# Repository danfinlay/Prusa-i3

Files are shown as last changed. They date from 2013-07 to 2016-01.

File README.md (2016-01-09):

# Dan's Prusa i3 Variant

I use this repository to store all the information I need on my 3D printer, an aluminum [Prusa i3](http://reprap.org/wiki/Prusa_i3), modified from a kit sold by *XS's Ink*, that I bought off Craigslist from a guy who had gave up at getting it working.

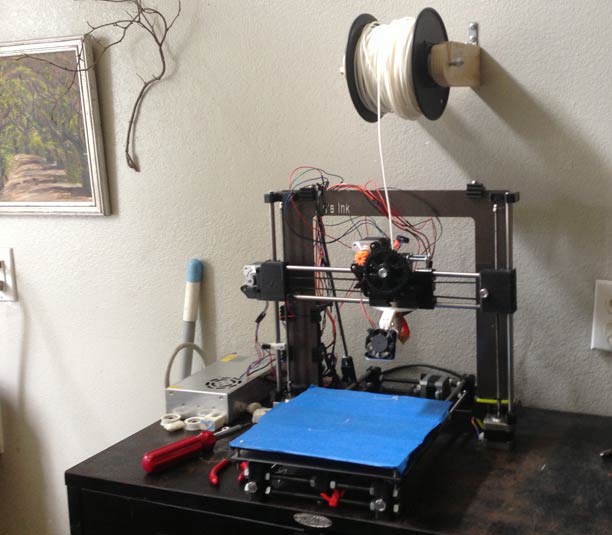
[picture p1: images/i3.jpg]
My printer


 - Model files to print the physical body.
 - Firmware files for flashing an Arduino (in my case, a [Sanguinololu 1.3a](https://github.com/mosfet/Sanguinololu/tree/master/rev1.3a))
 - Calibration files for use with [Slic3r](http://slic3r.org/).
 - Eventually I hope to add details on my OctoPrint server, maybe a Chef recipe. For now I have an SD image I clone, which is a bit bloated for version control.

## Physical Information

 - Size: 200mm cubed
 - Type: Aluminum framed body
 - Belt type: GT2 (2mm toothed robotics belt).
 - Extruder:  [Greg's Wade Extruder](http://www.thingiverse.com/thing:65939).
 - Nozzle: 0.5mm [Budaschnozzle 2.0](https://www.lulzbot.com/support/budaschnozzle-20) with 1.75mm PTFE tube modification for printing 1.75mm filament (I use PLA).
 - Bed leveling system: 3-point leveling, generally adjusted during the skirt-printing that occurs before every print when using the included Slic3r calibration bundle.

## Beware below!

Below is a pasted and only minorly cleaned up text file that I used to keep notes while I was originally calibrating the machine.

## Notes

serial frequency: 115200

micro step = 16x
full steps per revolution = 200
*This seems to be outdated, I use GT2 belts now:*
T5 belt (5mm) : http://www.sdp-si.com/D265/PDF/D265P1032.pdf
12 teeth on x & y motor gears

XY STEPS: 53

Z axis: M5 threaded rod (0.80 pitch).

Z STEPS: 4000
(un-micro-stepped gives us 0.08mm per step, the safest increment)
Set current z to 0: G92 Z0

### Valid layer height options
```javascript
for (var i = 0.2; i < 0.4; i+=0.08) { console.log(i); }
```
 - 0.2
 - 0.28
 - 0.36
 - 0.44

### Wade's Geared Extruder details:

hob diameter: 7.25mm
small gear teeth: 10
big gear teeth: 43

E STEPS: 605

Uses an 608 bearing on a M8x20 grub screw

Initial default line width: 0.85
Actual average fill width:  0.71+0.78+0.75 =AVERAGE=

theoretical/measured = 1.1333, then 1.25, now trying 1.5 just to try something crazy.  First 3 all gave around 0.75mm average, 1.5 gave around .93

Asked to extrude 30mm, instead extruded 26.56mm

Previous E Steps: 605
Number of steps tested: 605*30=18150
New E Steps: 18150/26.56mm = 683.3584337349398

Y axis was printing a bit small.  Printed a 25x25mm thing, y axis only gave 23.67, so I changed y steps per unit to 56.33, an increase of about 5%.

M303 E-0 C10 S190

## PID Calibrations

### Original J-Head Nozzle PID Calibration:
####With fan:
```C
  #define  DEFAULT_Kp 22.2
  #define  DEFAULT_Ki 1.08
  #define  DEFAULT_Kd 114
```

### Budaschnozzle 2.0 PID Calibration:
####Without fan:
 - Kp: 32.33
 - Ki: 1.55
 - Kd: 168.97

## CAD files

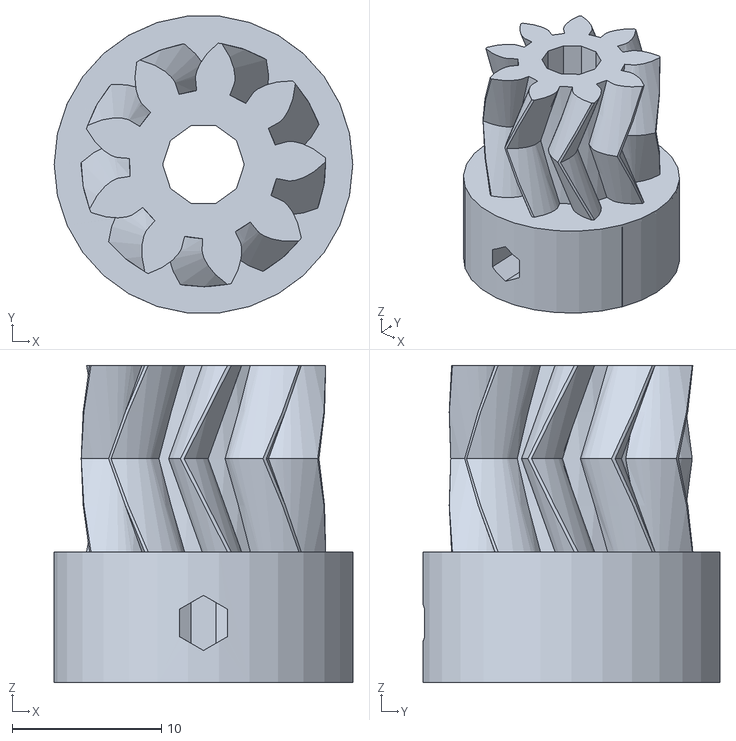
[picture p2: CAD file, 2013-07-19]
Printables/Extruder/Extruder-Gears-Herringbone/smallgearmod_fixed.stl
20.0 x 19.9 x 21.2

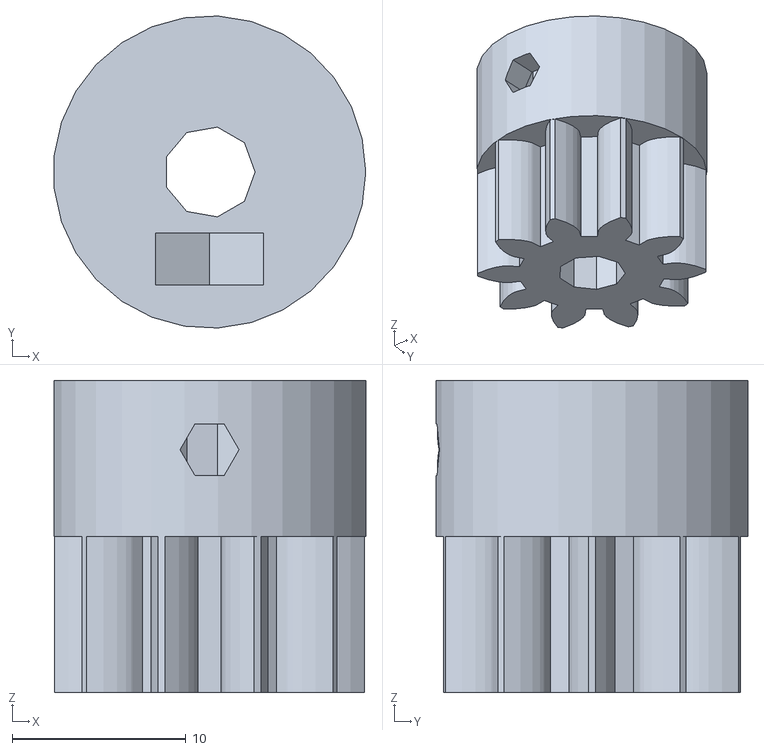
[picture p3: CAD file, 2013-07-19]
Printables/Extruder/Extruder-Gears-Spur/small_gear.stl
17.9 x 18.0 x 18.0

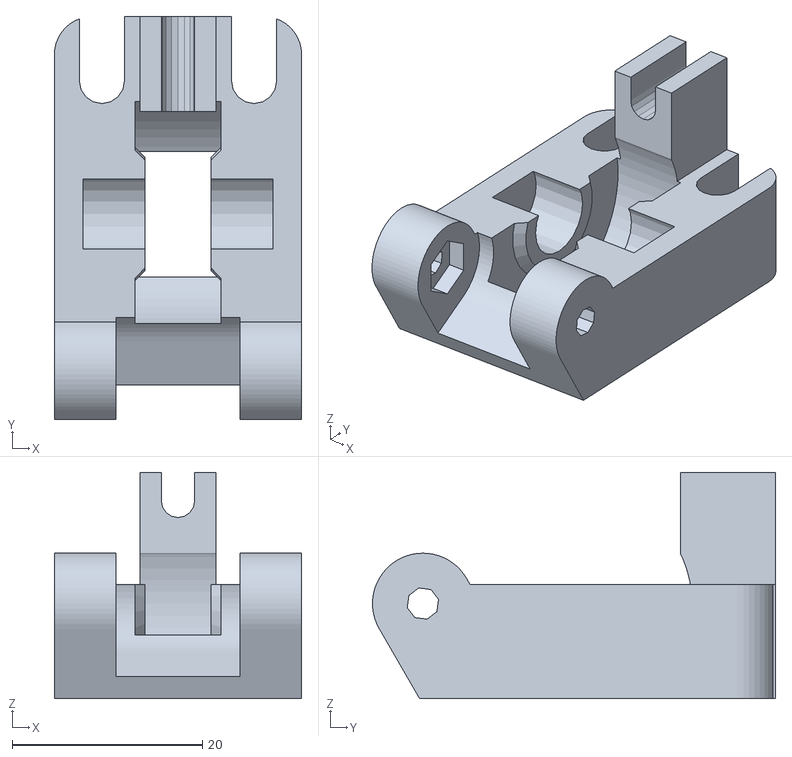
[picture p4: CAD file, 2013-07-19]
Printables/Extruder/superaccessible-idler.stl
26.0 x 42.4 x 23.8

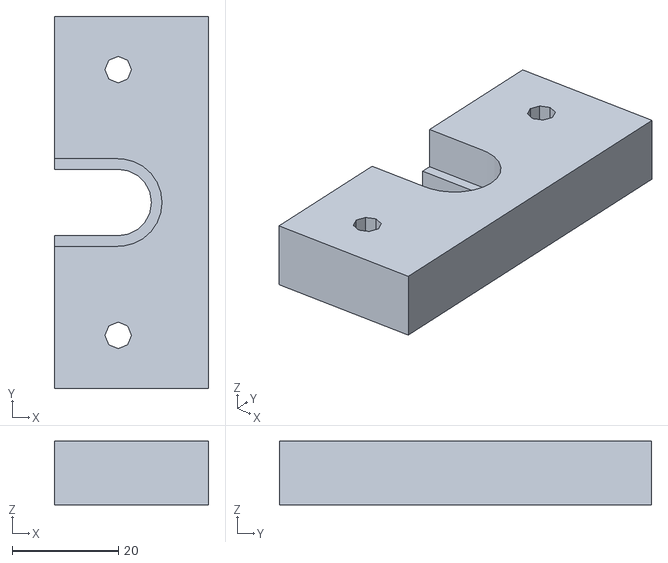
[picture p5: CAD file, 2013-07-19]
Printables/groovemount.stl
29.0 x 70.0 x 12.0

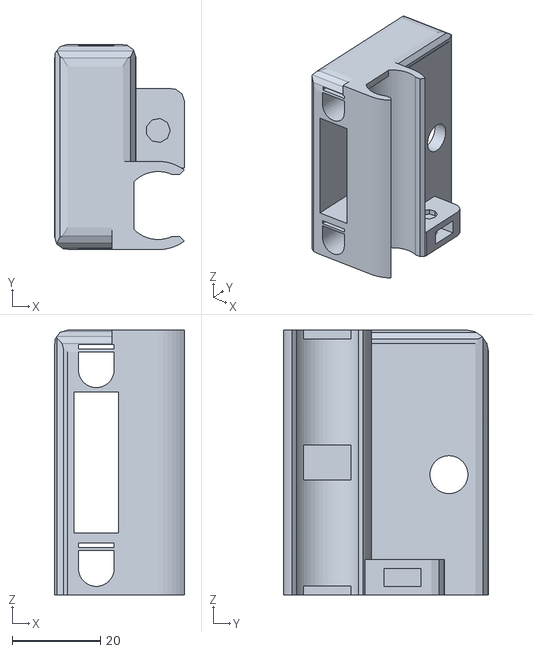
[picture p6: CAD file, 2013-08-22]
Printables/x-end divded/non-motor-side.stl
29.5 x 46.5 x 60.0

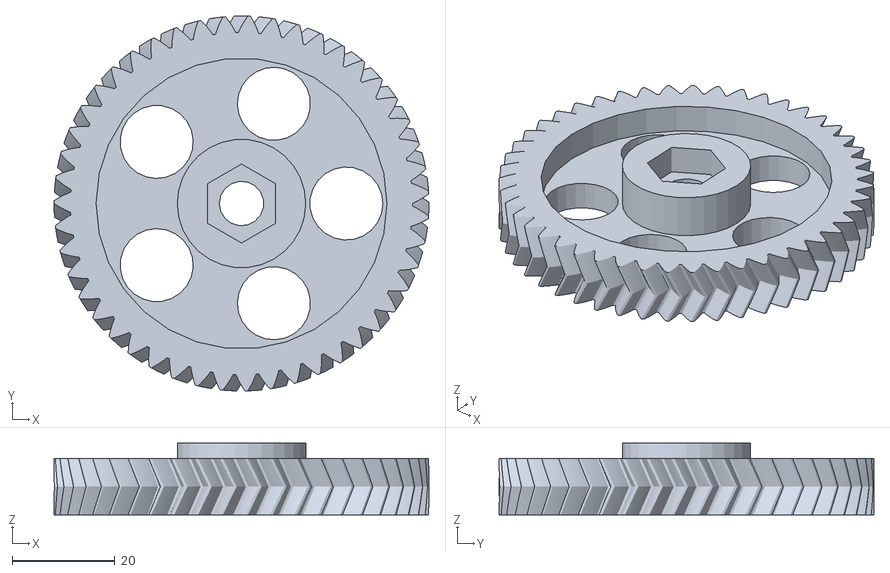
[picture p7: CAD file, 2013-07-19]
Printables/Extruder/Extruder-Gears-Herringbone/biggearmod_fixed.stl
73.0 x 73.0 x 14.0

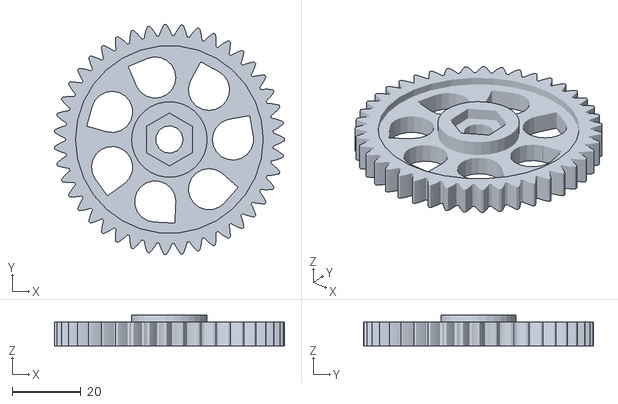
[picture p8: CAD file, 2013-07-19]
Printables/Extruder/Extruder-Gears-Spur/large_gear.stl
66.9 x 67.0 x 9.00

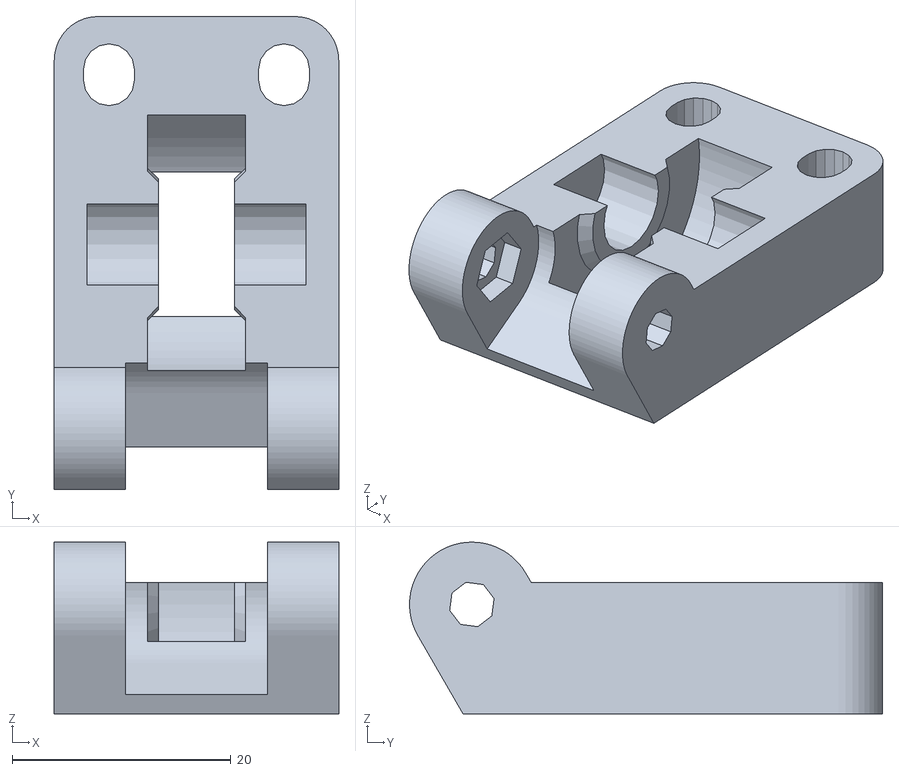
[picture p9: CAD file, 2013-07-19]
Printables/Extruder/idler.stl
26.0 x 43.2 x 15.7

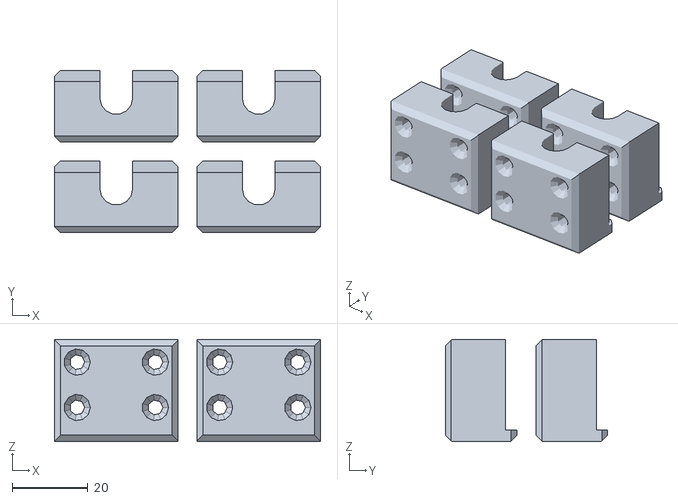
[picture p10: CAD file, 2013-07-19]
Printables/y-axis-bracket.stl
70.4 x 43.0 x 27.0

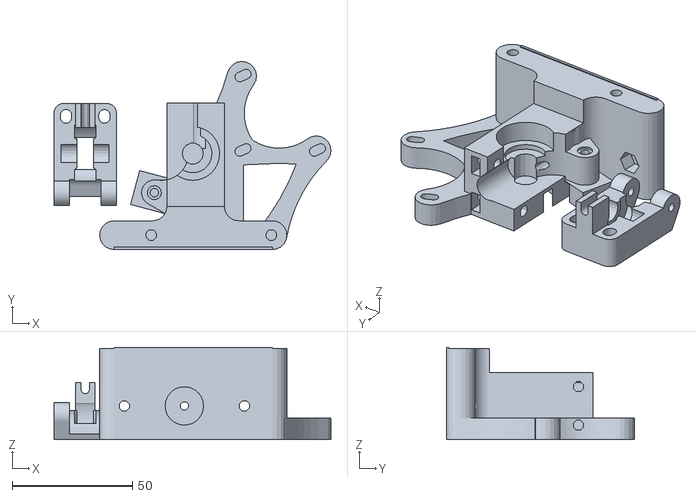
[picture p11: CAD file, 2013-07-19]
Printables/Extruder/gregs-wade-v3.stl
115.4 x 78.4 x 38.3

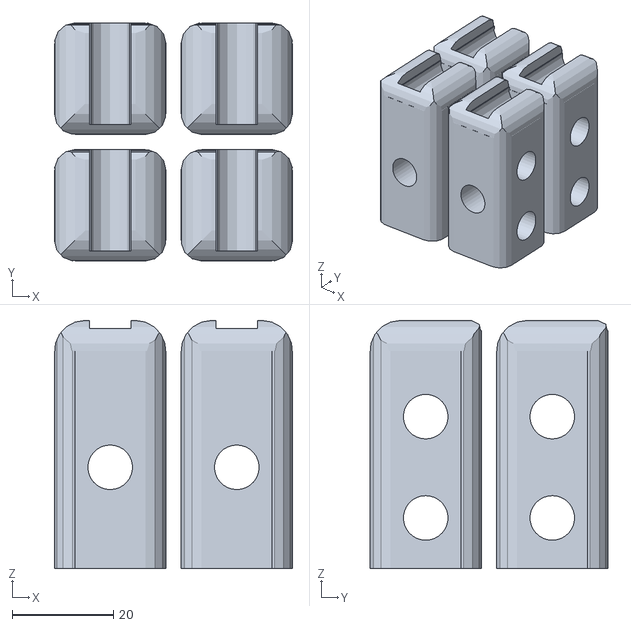
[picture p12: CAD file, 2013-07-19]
Printables/y-axis-corner.stl
47.0 x 47.0 x 49.0

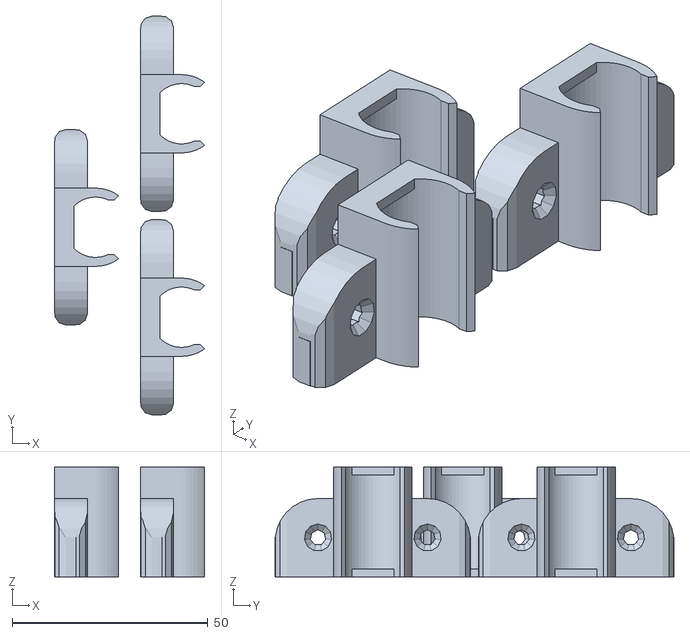
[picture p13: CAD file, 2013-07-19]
Printables/bushing.stl
38.4 x 102.0 x 28.0

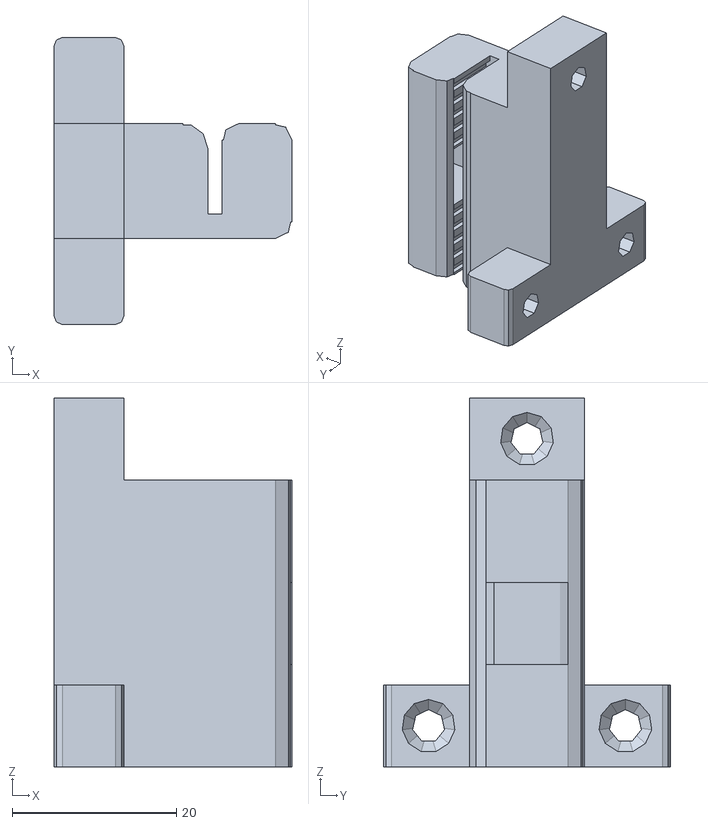
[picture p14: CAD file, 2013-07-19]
Printables/y-belt-holder.stl
29.0 x 35.0 x 45.0

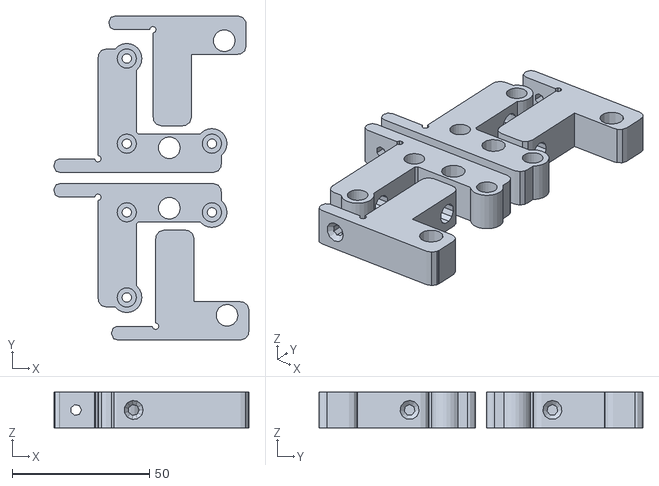
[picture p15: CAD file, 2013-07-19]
Printables/z-axis.stl
71.0 x 118.0 x 13.0

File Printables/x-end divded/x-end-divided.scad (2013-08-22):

module motorSideBoundingBox(){

	translate([35, 0, 30])
		cube([50, 150, 90], center=true);

}

module nonMotorSideBoundingBox(){

	//Haven't needed to print the motor side alone yet, so I haven't defined this.  If you need the motor side isolated, just copy paste and modify the above code, then substitute in this module's function call in the difference function below.
}


difference(){

	import("../x-end.stl");

	motorSideBoundingBox();

}

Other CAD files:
Printables/x-carriage.stl
Printables/x-end.stl

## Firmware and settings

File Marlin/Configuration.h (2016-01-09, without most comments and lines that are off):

#define CONFIGURATION_H
#define STRING_VERSION_CONFIG_H __DATE__ " " __TIME__ // build date and time
#define STRING_CONFIG_H_AUTHOR "(none, default config)" //Who made the changes.
#define SERIAL_PORT 0
#define BAUDRATE 115200
#define MOTHERBOARD 62
#define EXTRUDERS 1
#define POWER_SUPPLY 1
#define TEMP_SENSOR_0 7
#define TEMP_SENSOR_1 0
#define TEMP_SENSOR_2 0
#define TEMP_SENSOR_BED 0
#define MAX_REDUNDANT_TEMP_SENSOR_DIFF 10
#define TEMP_RESIDENCY_TIME 10  // (seconds)
#define TEMP_HYSTERESIS 3       // (degC) range of +/- temperatures considered "close" to the target one
#define TEMP_WINDOW     1       // (degC) Window around target to start the recidency timer x degC early.
#define HEATER_0_MINTEMP 5
#define HEATER_1_MINTEMP 5
#define HEATER_2_MINTEMP 5
#define BED_MINTEMP 5
#define HEATER_0_MAXTEMP 275
#define HEATER_1_MAXTEMP 275
#define HEATER_2_MAXTEMP 275
#define BED_MAXTEMP 150
#define PIDTEMP
#define BANG_MAX 256 // limits current to nozzle while in bang-bang mode; 256=full current
#define PID_MAX 256 // limits current to nozzle while PID is active (see PID_FUNCTIONAL_RANGE below); 256=full current
  #define PID_FUNCTIONAL_RANGE 10 // If the temperature difference between the target temperature and the actual temperature
  #define PID_INTEGRAL_DRIVE_MAX 255  //limit for the integral term
  #define K1 0.95 //smoothing factor withing the PID
  #define PID_dT ((16.0 * 8.0)/(F_CPU / 64.0 / 256.0)) //sampling period of the temperature routine
    #define  DEFAULT_Kp 32.33
    #define  DEFAULT_Ki 1.55
    #define  DEFAULT_Kd 168.97
#define MAX_BED_POWER 256 // limits duty cycle to bed; 256=full current
#define PREVENT_DANGEROUS_EXTRUDE
#define PREVENT_LENGTHY_EXTRUDE
#define EXTRUDE_MINTEMP 170
#define EXTRUDE_MAXLENGTH (X_MAX_LENGTH+Y_MAX_LENGTH) //prevent extrusion of very large distances.
#define ENDSTOPPULLUPS // Comment this out (using // at the start of the line) to disable the endstop pullup resistors
  #define ENDSTOPPULLUP_XMAX
  #define ENDSTOPPULLUP_YMAX
  #define ENDSTOPPULLUP_ZMAX
  #define ENDSTOPPULLUP_XMIN
  #define ENDSTOPPULLUP_YMIN
  #define ENDSTOPPULLUP_ZMIN
const bool X_ENDSTOPS_INVERTING = false; // set to true to invert the logic of the endstops.
const bool Y_ENDSTOPS_INVERTING = false; // set to true to invert the logic of the endstops.
const bool Z_ENDSTOPS_INVERTING = false; // set to true to invert the logic of the endstops.
#define X_ENABLE_ON 0
#define Y_ENABLE_ON 0
#define Z_ENABLE_ON 0
#define E_ENABLE_ON 0 // For all extruders
#define DISABLE_X false
#define DISABLE_Y false
#define DISABLE_Z false
#define DISABLE_E false // For all extruders
#define INVERT_X_DIR true    // for Mendel set to false, for Orca set to true
#define INVERT_Y_DIR false    // for Mendel set to true, for Orca set to false
#define INVERT_Z_DIR false     // for Mendel set to false, for Orca set to true
#define INVERT_E0_DIR false   // for direct drive extruder v9 set to true, for geared extruder set to false
#define INVERT_E1_DIR false    // for direct drive extruder v9 set to true, for geared extruder set to false
#define INVERT_E2_DIR false   // for direct drive extruder v9 set to true, for geared extruder set to false
#define X_HOME_DIR -1
#define Y_HOME_DIR -1
#define Z_HOME_DIR -1
#define min_software_endstops false //If true, axis won't move to coordinates less than HOME_POS.
#define max_software_endstops true  //If true, axis won't move to coordinates greater than the defined lengths below.
#define X_MAX_POS 200
#define X_MIN_POS 0
#define Y_MAX_POS 200
#define Y_MIN_POS 0
#define Z_MAX_POS 100
#define Z_MIN_POS 0
#define X_MAX_LENGTH (X_MAX_POS - X_MIN_POS)
#define Y_MAX_LENGTH (Y_MAX_POS - Y_MIN_POS)
#define Z_MAX_LENGTH (Z_MAX_POS - Z_MIN_POS)
#define MANUAL_X_HOME_POS 0
#define MANUAL_Y_HOME_POS 0
#define MANUAL_Z_HOME_POS 0
#define NUM_AXIS 4 // The axis order in all axis related arrays is X, Y, Z, E
#define HOMING_FEEDRATE {50*60, 50*60, 5*30, 0}  // set the homing speeds (mm/min)
#define DEFAULT_AXIS_STEPS_PER_UNIT   {53.33, 53.33, 4000, 604.96}  // My first set of calibration calculations
#define DEFAULT_MAX_FEEDRATE          {500, 500, 5, 25}    // (mm/sec)
#define DEFAULT_MAX_ACCELERATION      {9000,9000,100,10000}    // X, Y, Z, E maximum start speed for accelerated moves. E default values are good for skeinforge 40+, for older versions raise them a lot.
#define DEFAULT_ACCELERATION          2500    // X, Y, Z and E max acceleration in mm/s^2 for printing moves
#define DEFAULT_RETRACT_ACCELERATION  3000   // X, Y, Z and E max acceleration in mm/s^2 for r retracts
#define DEFAULT_XYJERK                20.0    // (mm/sec)
#define DEFAULT_ZJERK                 0.4     // (mm/sec)
#define DEFAULT_EJERK                 5.0    // (mm/sec)
#define PLA_PREHEAT_HOTEND_TEMP 18
#define PLA_PREHEAT_HPB_TEMP 70
#define PLA_PREHEAT_FAN_SPEED 255   // Insert Value between 0 and 255
#define ABS_PREHEAT_HOTEND_TEMP 240
#define ABS_PREHEAT_HPB_TEMP 100
#define ABS_PREHEAT_FAN_SPEED 255   // Insert Value between 0 and 255
#include "Configuration_adv.h"
#include "thermistortables.h"

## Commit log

2013-07-19 Added immediate needs.
    [x-carriage.stl, x-end.stl]
2013-07-19 Full kit, unchecked.
    [biggearmod_fixed.stl, bushing.stl, gregs-wade-v3.stl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]
2013-07-19 Added gear variants
    [biggearmod_fixed.stl, large_gear.stl, small_gear.stl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]
2013-07-19 Sorted out extruder, isolated its idler.
    [biggearmod_fixed.stl, gregs-wade-v3.stl, idler.stl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]
2013-07-19 Added quick-access guidler to extruder.
    [idler.stl, jonaskuehling_gregs-wade-v3_idler-only.stl]
2013-07-19 Included both guidler options as I'm undecided.
    [idler.stl, superaccessible-idler.stl]
2013-08-22 Split the x-end stl via an openscad file to allow printing them individually.
    [non-motor-side.stl, x-end-divided.scad]
2016-01-09 Added slic3r calibration file
2016-01-09 Added Marlin firmware
    [Configuration.h, Configuration_adv.h]
